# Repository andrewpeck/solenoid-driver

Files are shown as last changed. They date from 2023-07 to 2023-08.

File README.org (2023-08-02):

** Single Channel Solenoid Driver

#+attr_org: :width 500px
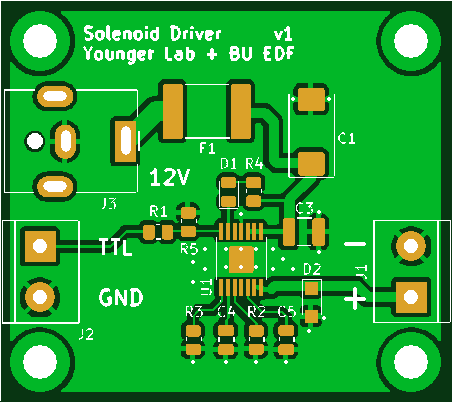
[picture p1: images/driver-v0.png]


A prototype single channel solenoid driver was developed for testing.

It is contained in the ~driver-v0~ folder.

We will have 3 manifolds with 8 of these in a row that need to be driven with 12V and signalled with a TTL line. All the manifolds will act in unison.

 - https://www.theleeco.com/product/lhd-series-2-way-control-solenoid-valve/
 - 3 boards, 8 channels each
 - 8 TTL inputs + GND
 - 8 12V outputs
 - 12V input on barrel jack
   - Plug:
     - https://www.digikey.com/en/products/detail/globtek-inc/CRP11856F00/16515770
     - Cable Assembly 2.1mm ID, 5.5mm OD Jack, Right Angle to Wire Leads Round 6.0' (1.83m)
   - Jack:
     - https://www.digikey.com/en/products/detail/cui-devices/PJ-063AH/2161208
     - PJ-063AH Power Barrel Connector Jack 2.10mm ID (0.083"), 5.50mm OD (0.217") Through Hole, Right Angle
 - LHDB1242115H
 - Spike+hold voltage: 12, 7.2
 - LOHM RATE** (Cv): 1500 Lohms (0.013)
 - Power Consumption At Hold Voltage (mW): 310
 - Response time: 10 ms Max

|----+-----------+-----+----------------------+--------------------+---------------------------|
|  # | Reference | Qty | Value                | PartNum            | Mfg                       |
|----+-----------+-----+----------------------+--------------------+---------------------------|
|  1 | C1        |   1 | 47uF                 | T491X476K035AT     | Kemet                     |
|  2 | C3        |   1 | 10uF                 | CL32A106KLULNNE    | Samsung Electro-Mechanics |
|  3 | C4        |   1 | 0.18 uF              | 08053C184KAT2A     | KYOCERA AVX               |
|  4 | C5        |   1 | 470pF                | C0805C471K5RAC7800 | Kemet                     |
|  5 | D1        |   1 | LED                  | 150080RS75000      | Wurth                     |
|  6 | D2        |   1 | PMEG10010ELRX        | PMEG10010ELRX      | Nexperia                  |
|  7 | F1        |   1 | 0ZCF0125FF2C         | 0ZCF0125FF2C       | Bel Fuse                  |
|  8 | J1, J2    |   2 | Screw_Terminal_01x02 | 282837-2           | TE                        |
|  9 | J3        |   1 | Barrel_Jack          | PJ-063AH           | CUI                       |
| 10 | R1        |   1 | 49R9                 | RC0805FR-0749R9L   | Yageo                     |
| 11 | R2        |   1 | 191k                 | RC0805FR-07191KL   | Yageo                     |
| 12 | R3        |   1 | 162k                 | RC0805FR-07162KL   | Yageo                     |
| 13 | R4, R5    |   2 | 4k7                  | RC0805JR-074K7L    | Yageo                     |
| 14 | U1        |   1 | DRV104PWP            | DRV104PWP          | TI                        |
|----+-----------+-----+----------------------+--------------------+---------------------------|

** Octal Channel Driver

** Dual Channel Complementary Driver

We will also have a pair of these valves that need to be driven by a single TTL
line in opposition (if one is in state A the other should be in state B).
 - LHDA1231415H
 - https://www.theleeco.com/product/lhd-series-3-way-control-solenoid-valve/
 - One TTL input  + GND
 - Two 12V complementary outputs

The solenoids should be driven with a high-side switch using a peak and hold circuit.

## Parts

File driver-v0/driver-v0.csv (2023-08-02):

Reference | Value | Footprint | Datasheet | Mfg | PartNum | Sim.Device | Sim.Pins | Qty
C1 | 47uF | Capacitor_Tantalum_SMD:CP_EIA-7343-43_Kemet-X_Pad2.25x2.55mm_HandSolder |  | Kemet | T491X476K035AT |  |  | 1
C3 | 10uF | Capacitor_SMD:C_1210_3225Metric | ~ | Samsung Electro-Mechanics | CL32A106KLULNNE |  |  | 1
C4 | 0.18uF | Capacitor_SMD:C_0805_2012Metric | ~ | KYOCERA AVX | 08053C184KAT2A |  |  | 1
C5 | 470pF | Capacitor_SMD:C_0805_2012Metric | ~ | Kemet | C0805C471K5RAC7800 |  |  | 1
D1 | LED | LED_SMD:LED_0805_2012Metric | ~ | Wurth | 150080RS75000 |  |  | 1
D2 | PMEG10010ELRX | Diode_SMD:Nexperia_CFP3_SOD-123W | ~ | Nexperia | PMEG10010ELRX | D | 1=K 2=A | 1
F1 | 0ZCF0125FF2C | Fuse:Fuse_2920_7451Metric | ~ | Bel Fuse | 0ZCF0125FF2C |  |  | 1
J1, J2 | Screw_Terminal_01x02 | TerminalBlock:TerminalBlock_bornier-2_P5.08mm | ~ | TE | 282837-2 |  |  | 2
J3 | Barrel_Jack | Connector_BarrelJack:BarrelJack_CUI_PJ-063AH_Horizontal | ~ | CUI | PJ-063AH |  |  | 1
R1 | 49R9 | Resistor_SMD:R_0805_2012Metric | ~ | Yageo | RC0805FR-0749R9L |  |  | 1
R2 | 191k | Resistor_SMD:R_0805_2012Metric | ~ | Yageo | RC0805FR-07191KL |  |  | 1
R3 | 162k | Resistor_SMD:R_0805_2012Metric | ~ | Yageo | RC0805FR-07162KL |  |  | 1
R4, R5 | 4k7 | Resistor_SMD:R_0805_2012Metric | ~ | Yageo | RC0805JR-074K7L |  |  | 2
U1 | DRV104PWP | driver-v0:IC_TPS27S100BPWPR |  | TI | DRV104PWP |  |  | 1

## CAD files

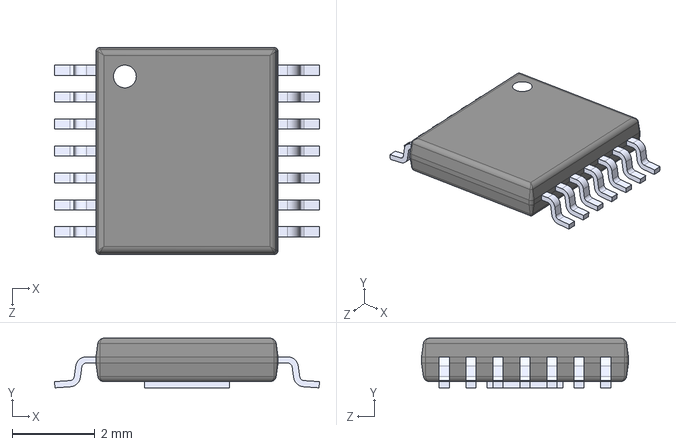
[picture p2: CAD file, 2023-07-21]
driver-v0/DRV104PWP.step
6.40 x 1.20 x 5.00 mm

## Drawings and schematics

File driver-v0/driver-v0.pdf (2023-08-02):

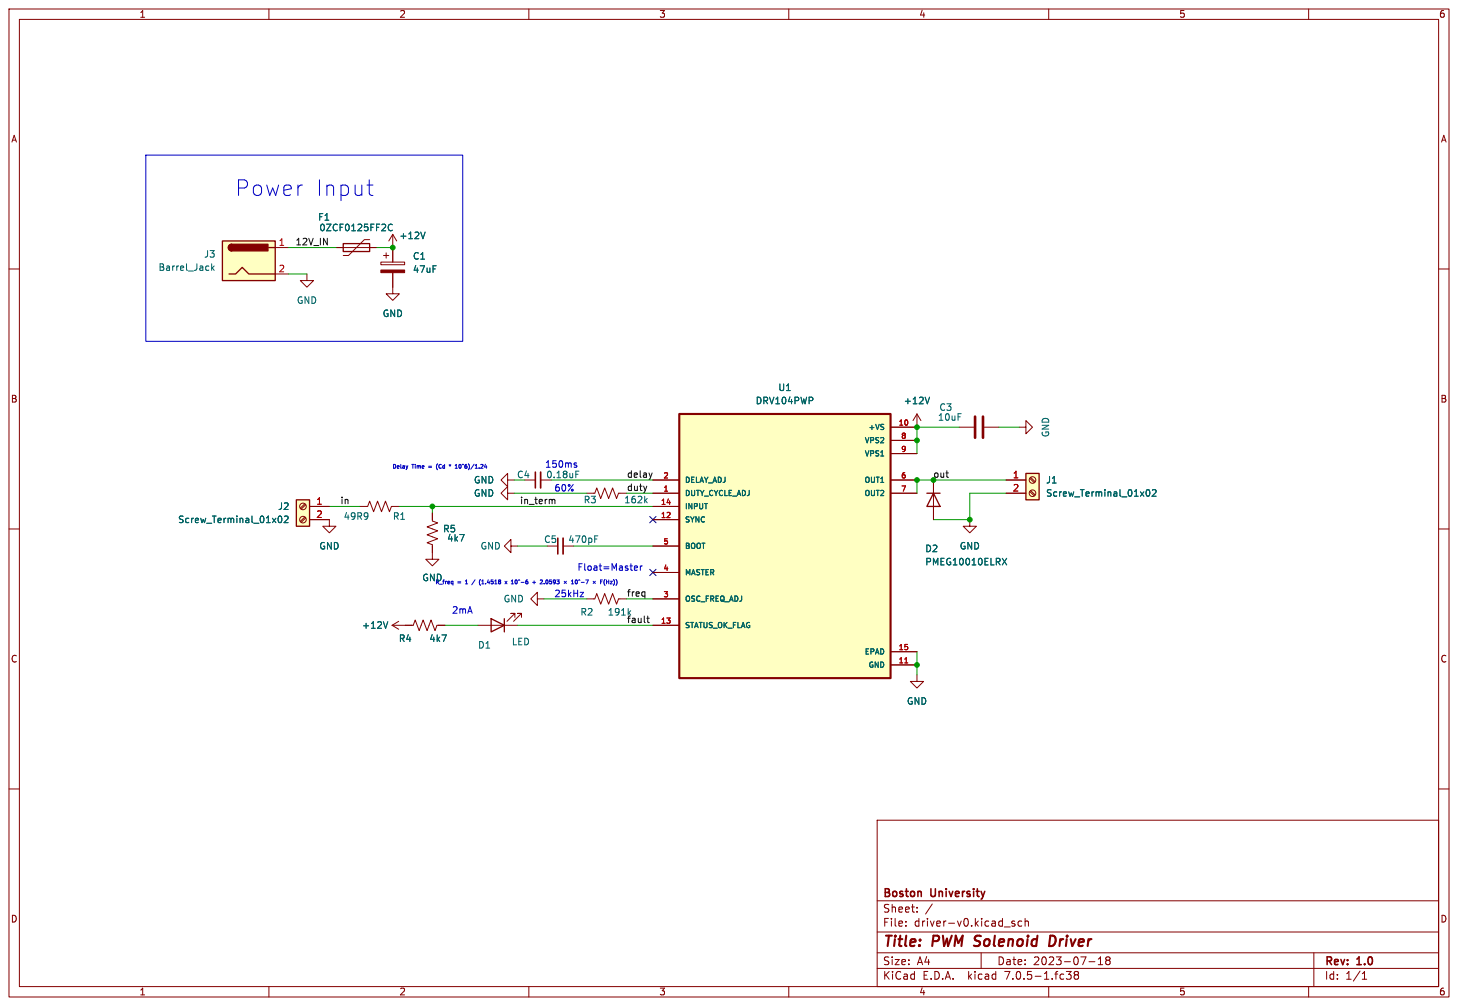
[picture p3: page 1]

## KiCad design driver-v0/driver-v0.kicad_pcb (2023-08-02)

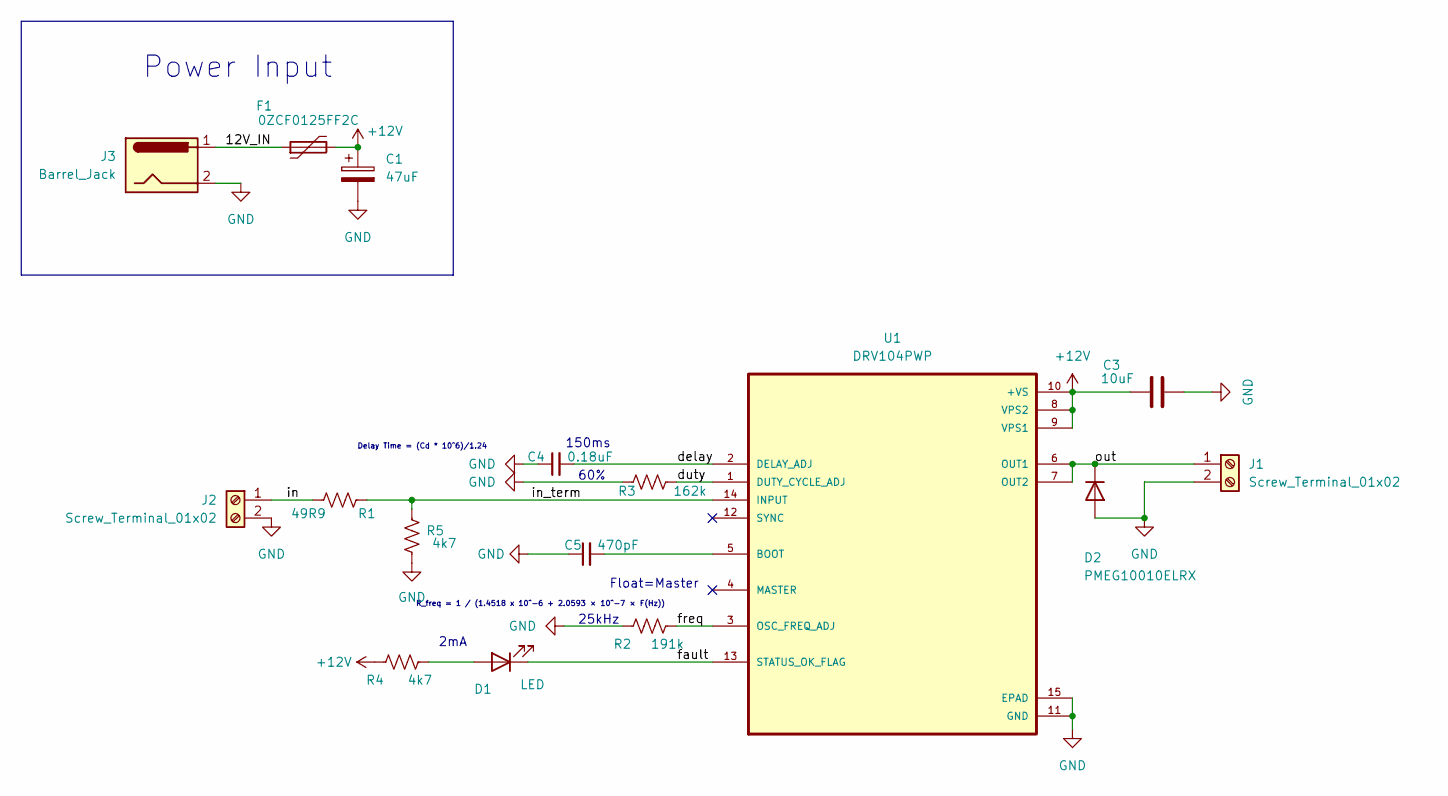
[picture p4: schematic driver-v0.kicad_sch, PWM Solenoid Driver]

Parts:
C1: 47uF; CP_EIA-7343-43_Kemet-X_Pad2.25x2.55mm_HandSolder; PartNum T491X476K035AT
C3: 10uF; C_1210_3225Metric; PartNum CL32A106KLULNNE
C4: 0.18uF; C_0805_2012Metric; PartNum 08053C184KAT2A
C5: 470pF; C_0805_2012Metric; PartNum C0805C471K5RAC7800
D1: LED; LED_0805_2012Metric; PartNum 150080RS75000
D2: PMEG10010ELRX; Nexperia_CFP3_SOD-123W; PartNum PMEG10010ELRX
F1: 0ZCF0125FF2C; Fuse_2920_7451Metric; PartNum 0ZCF0125FF2C
J1, J2: Screw_Terminal_01x02; TerminalBlock_bornier-2_P5.08mm; PartNum 282837-2
J3: Barrel_Jack; BarrelJack_CUI_PJ-063AH_Horizontal; PartNum PJ-063AH
R1: 49R9; R_0805_2012Metric; PartNum RC0805FR-0749R9L
R2: 191k; R_0805_2012Metric; PartNum RC0805FR-07191KL
R3: 162k; R_0805_2012Metric; PartNum RC0805FR-07162KL
R4, R5: 4k7; R_0805_2012Metric; PartNum RC0805JR-074K7L
U1: DRV104PWP; IC_TPS27S100BPWPR; PartNum DRV104PWP

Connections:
+12V: C1.1, C3.1, F1.2, R4.1, U1.8 (VPS2), U1.9 (VPS1), U1.10 (+VS)
/12V_IN: F1.1, J3.1
/delay: C4.2, U1.2 (DELAY_ADJ)
/duty: R3.2, U1.1 (DUTY_CYCLE_ADJ)
/fault: D1.1 (K), U1.13 (STATUS_OK_FLAG)
/freq: R2.2, U1.3 (OSC_FREQ_ADJ)
/in: J2.1, R1.1
/in_term: R1.2, R5.2, U1.14 (INPUT)
/out: D2.1 (K), J1.1, U1.6 (OUT1), U1.7 (OUT2)
GND: C1.2, C3.2, C4.1, C5.1, D2.2 (A), J1.2, J2.2, J3.2, R2.1, R3.1, R5.1, U1.11 (GND), U1.15 (EPAD)
unnamed: D1.2 (A), R4.2
unnamed: C5.2, U1.5 (BOOT)

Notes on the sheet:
25kHz
Power Input
Float=Master
60%
R_freq = 1 / (1.4518 x 10^−6 + 2.0593 × 10^−7 × F(Hz))
2mA
150ms
Delay Time = (Cd * 10^6)/1.24

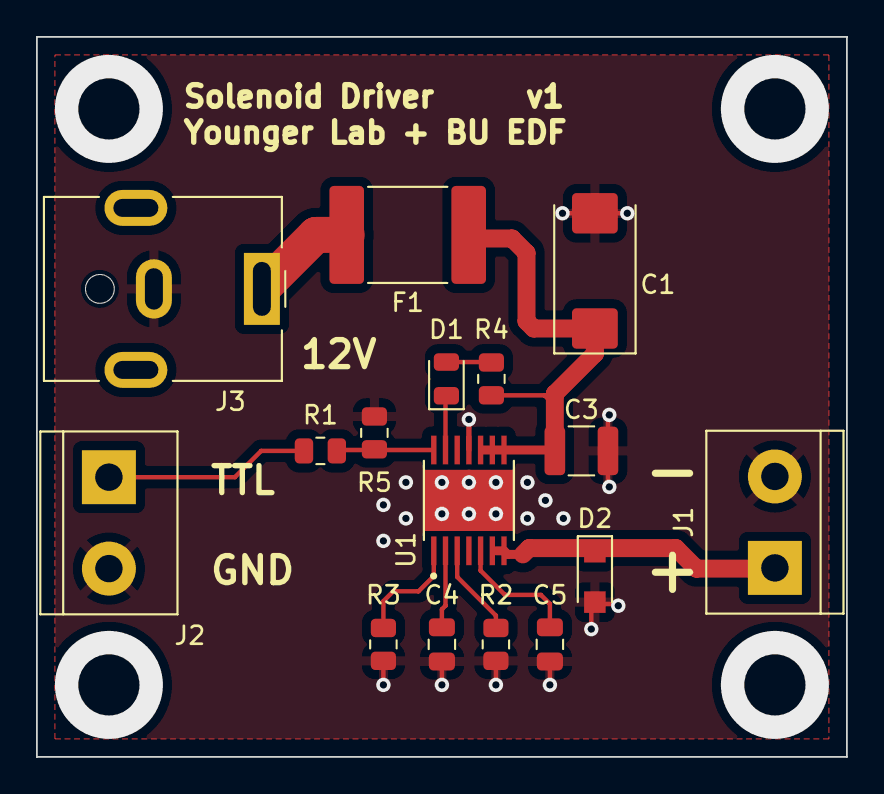
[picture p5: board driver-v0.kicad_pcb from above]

Board: 2 copper layers, 45.0 x 40.0 mm, 16 parts (0 on the bottom side), 12 nets.

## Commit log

2023-07-21 init solenoid driver
    [DRV104PWP.step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]
2023-07-25 fix bom
    [driver-v0.csv, driver-v0.kicad_sch]
2023-07-26 Add pdf schematic
2023-08-02 fix: change peak width from 150 us to 150 ms
    max switching time is 100 ms
    [driver-v0.csv, driver-v0.kicad_pcb, driver-v0.kicad_sch]
